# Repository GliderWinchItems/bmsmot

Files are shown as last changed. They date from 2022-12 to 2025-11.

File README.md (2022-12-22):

# bmsmot
This board is the control for the BMS (battery monitoring system) for one string of batteries; the contactor function, thermistor inputs for motor coolant, and output drive for enables, relays, and external high current FET sub-boards. A STM32F446RET6 is the main processor on this board.

The contactor function measures the high voltage using a STM32L431RCT6, ground isolated and communicates readings to the main processor via uart with opto-isolator. It also measures battery string current using an external Hall-effect sensor.

The main board provides for the CAN bus cabling to the BMS modules to loop back and apply +12v current to both ends of the CAN cabling, as well as in & out connectors for other nodes on the CAN bus. Provision is for a second CAN bus.

The software provides the EMC (Energy Management Control) and MMC (Motor Management Control) functions for one battery/motor installation.

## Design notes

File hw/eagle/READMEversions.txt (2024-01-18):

READMEversions.txt
12/27/23

pwrfet

1. Initial board (5 boards ordered): 

  TLP151A blew up twice, 

  AUIRS2110S didn't work...twice. 

  Motor transients appeared to cause at least
one blowup.

  Hacked (ugly) to add 12v regulator--
  - No fet driver
  - SB540 diode flyback
  - works

2. pwrfet-v2 (5 boards ordered)

First version but added 
  12v regulator (two options)
  DGD05463 FET driver
  Misc improvements of caps foot prints, etc.

 Polarity incorrect on fet driver incorrect.
  Solution 1: motor hi/lo junction to ground
   instead of +12 to hi/lo junction.
  Solution 2: remove fet3 and drive TLP151
    directly from bmsmot board's 74HCT125.

3. pwrfet-v3 (5 boards ordered)

V2 revised for ADP3110 or ADP3120 FET driver
which is a SOT package

Polarity incorrect to fet driver (same as v2).
 1st board: removed driver and hi side fet,
   diode flyback. 
   TLP151 drives lo side fet directly.

4. pwrfet-v4 (layout not complete as of 12/27/23)

V3 revised to add 74HCT02 (quad NOR) and AP311 comparator
to limit max current in low-side FET source.

5. pfuart & pfCAN

New repo started for a version using a STM32L431.
See: GliderWinchItems/isopwrfet.

  pfCAN layout complete (240109) but not reviewed.

  pfuart not started work.

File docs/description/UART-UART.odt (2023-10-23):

Goal: Send/receive CAN msgs over UART-UART comm connection between two processors.

Conditions & Restrictions:

1. 1 Mbps rate

2. No char-by-char interrupt allowed (which means only DMA)

3. Fixed block/packet size (19 bytes)

- start byte

- 16 data bytes (CAN struct: ID, DRC, Payload)

- check byte

- stop byte

4. Start/Stop phasing

- Initialization may begin in the middle of a packet being received, and possibility is high.

- Noise may cause start/stop phasing may be lost during operation, but possibility is low.

5. Check byte error

- Used to determine if the packet is legitimate when a stop byte 18 bytes following a start byte is encountered.

- Make use of STM32 hardware CRC peripheral.

6. Minimize packets lost when re-syncing.

General scheme--

Make use of STM32F446 double buffering DMA.

- Two registers for start of storing USART2-RX: S5MOAR S5SM1AR

Before enable both registers may be written.

After enable the register not being used to store can be written. The CT bit 19 in the S5CR (Control Register)

0: current target memory is Memory 0 (addressed by the DMA_SxM0AR pointer)

1: current target memory is Memory 1 (addressed by the DMA_SxM1AR pointer)

- Set the buffer size (S5NDTR) to 2*packet size (i.e. 2*19=38).

- Set circular mode. Pointer and size reloads when end of buffer reached.

- Enable Half and Full interrupts. This will give an interrupt at every 19 bytes stored, i.e. the packet size.

If the start of packet is in synch so that the first byte of the buffer and byte following the half buffer are start bytes and the stop and check bytes are OK, then the DMA will give an interrupt every time a complete CAN msg has been received. The half and full interrupts allow the previously stored ½ buffer to be processed while new incoming bytes are being stored. Basically, an interrupt after each CAN msg has been received.

The tricky problem is how to get the DMA in sync with the start of the packets without resorting to char-by-char uart interrupts.

To do char-by-char interrupts requires the interrupt priority to be higher than the RTOS timer, since it could preempt handing a char interrupt and cause on overrun. Also, the shear speed, especially if there are two UARTs running is a heavy processor load. One char for USART2 at 1 Mbps is 10 usec. Hence, reliance of the DMA is required.

To resync, the plan is to make use of the option to change the address where the buffer pointer not currently in use can be updated.

Suppose the buffers are laid out as follows--

#define B_START 0x36; // Unlikely noise triggered char

#define B_STOP ~START

struct UCAN

{

uint8 start;

struct CANRCVBUF

uint16 pec15

uint8 stop;

};

struct UCAN uubuf[2*3];

Two pairs of UCAN buffers.

Hmm, does there need to be an overrun, i.e. “3”.

S5M0AR = &uubuf[0];

S5M1AR = &uubuf[2];

S5NDTR = sizeof(struct UCAN);

06/08/2023 UART-UART communication Page 2

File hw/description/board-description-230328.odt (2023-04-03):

Overview

The following describes the bmsmot pcb design & layout at this stage of development (March 31 2023). The eagles files can be found in--

~/GliderWinchItems/bmsmot/hw/eagle/bmsmot

Only parts for the needed features can be installed, and the value of resistors, capacitors, etc., the following are tentative and depend upon the assignments.

This board can be configured to handle the EMC/MMC or PSN Power Supply Node (PSN).

For the EMC/MMC the following is supplied

- BMS CAN 12v power switched

- BMS CAN Master Reset switched

- Contactor coil #1 energize

- Contactor coil #2 energize

- Contactor HV measurements

- Contactor current measurements

- Cooling pump control (PWM)

- Heat exchanger fan/blower control (PWM)

- DMOC fan control (PWM)

- SCP 12v supply input on/off relay

- RCP 12v supply input on/off relay

- SCP 12v supply output relay on/off

- AC/DC input power select relay

- Coolant inlet temperature thermistor

- Coolant outlet temperature thermistor

- Ambient temperature thermistor

- Float battery string leakage detection

For PSN-

- Main 12v battery on/off

- Air compressor on/off

- Air pressure measurement (ADC)

- AC voltage measurement

- Mains|generator select

- RTC wakeup

- Rotating beacon

Other provisions-

- LEDs

LED1 - Green: 12v switched power

LED2 – Green: PB12 i/o-F446

LED3 – Red: PB13 i/o-F446

LED4 – Green: PB0 i/o- L431

LED5 – Red: PB1 i/o-L431

LED6 – Red: NFET5-PA5-Master Reset or Master Reset pushbutton (BMS loop)

- EMC/MMC-local to EMC-master UART-UART communication option

- Pushbuttons

RESET – F446

RESET – L431

Master-Reset BMS loop

- Header for encoder (TIM2)

- ADC: F446: six with headers

Four with 2 pin headers: 10K pullup w 0.1 cap to gnd

+12v power measurement (no header)

One with 2 pin header: Series resistor, 10K pullup w 0.1 cap to gnd

One with 3 pin header: Resistor divider (5V→3.3V) w big cap to gnd.

- ADC: F446: 12v switched power voltage measurement

- spare FET output

JP20 - 2-pin header, NFET-SUB14, PB3- T2C2

- Xtals:Oscillators

32 Khz RTC

16 MHz system

Board size

140 x 100 mm

Mounting hole (dia 3.2 mm) positions--

3.2 3.2

136.8 3.2

136.8 96.8

3.2 96.8

80.0 70.0

12v power input

(Upper-left) the 12v power is connected via a Power Pole connector pair with a pigtail, or spade lugs. There are two large holes for strain relief for the Power Pole option. The pigtail solders into holes in the middle of the spade lug thu-holes. This called the “raw” 12v power.

Possible power PFETs provide polarity protection--

DMP3007SCG-7

PJQ4403

The input voltage will exceed the Vgs for a DMP3007 so a 10v zener used. The PJQ4403 has a +/- 20 Vgs so the zener could be omitted, however the PJQ4403 has a lower continuous Id.

The polarity protection PFET limits the total current to about 4a. That includes the BMS loop and any +12v loads one the headers, e.g. relays, plus the processor load. Each of the BMS low current chargers can draw about 6W. A string of six requires 36W, or about 3a at 12v.

12V power protected

The polarity protected output of the input PFET is “+12V” on the schematic. This feeds into a second PFET that can switch the 12v on/off.

12V power switched

The switched 12v feeds the BMS CAN bus loop, and most of the BMS board.

When configured for a Power Supply Node (PSN) the 12v battery would power this board and if the second PFET is off the only load on the battery is the 5v regulator and processor. The processor would be in shutdown mode so its draw would be in the 1-10 ua range. The linear regulator is 1.8 ua typical. To wake the system, either a short to gnd via the 2-pin header JP19, or NFET1 turned on via the processor RTC and coin-cell.

Configured for the EMC/MMC the switched 12v can turn the BMS CAN bus 12v on/off via the NFET and i/o pin PC13.

FET outputs (SUBx)

Eight FET driven outputs are labeled HDR-SUB1 through HDR-SUB8. Each output has a JST 4 pin keyed header (gnd, fet drain, +5v, +12v). Provision is for flyback diodes to 5v, 12v, and a pullup resistor. The FET, diode/resistor, installed depends on the usage of the output.

Each FET is driven from an i/o pin that can be assigned to a timer channel so that PWM can be applied. Some outputs share the same timer which means that the PWM frame duration would be common to all the channels on that timer doing PWM.

pcb label: i/o - timer:channel

HDR-SUB1: PB2 - T2C4

HDR-SUB2: PB10 - T2C3

HDR-SUB3: PB14 - T12C1

HDR-SUB4: PB15 - T12C2

HDR-SUB5: PC6 – T3C1, T8C1

HDR-SUB6: PC7 – T3C2, T8C2

HDR-SUB7: PC8 – T3C3, T8C3

HDR-SUB8: PC9 – T3C4, T8C4

Note: if the encoder input is used (TIM2) there could be some time frame issues if HDR-SUB1 & 2 assignments are for PWMing.

FET outputs (HDRx)

Four outputs driven by a 74VHCT125 buffers can drive external sub-boards with power fets for high current switching. These inputs to the buffers are i/o pins that have associated timers.

HDRXX1: PA10 - T1C3

HDRXX2: PA11 - T1C4

HDRXX3: PA9 - T1C2

HDRXX4: PA8 - T1C1

ADC ‘F446

Eight ADC channels with headers used.

Four inputs have 10K pullups and 0.1u cap to gnd for thermistors.

JP1 – PC0-ADC123-IN10

JP8 – PC1-ADC123-IN11

JP9 - PC2-ADC123-IN12

JP10 - PC3-ADC123-IN13

One has a series resistor added which could be used for voltage divider by installing a resistor in place of the 0.1 cap. It could be used for input of an external switch or contacts; the 0.1 cap could be replaced with a zener if voltage protection is needed, etc.

JP22 -PC4-ADC12-IN14

One with a keyed 3 pin JST connector, JP24 (gnd, signal, +5v), for air pressure sensor. The +5 is from the dc-dc switcher for the main board so it has some switching ripple on it. The signal line has a resistor divider (R36|R19) for reducing the max voltage to 3.3v, and 4.6u 0603 cap (C38) can be used to help the noise, along with software filtering.

JP24 – PC5-ADC12-IN15

Battery string leakage detection

To keep the battery string from accumulating charge and drifting too far above/below the system ground to where the isolation components (e.g. CAN interfaces and dc-dc converters) voltage isolation will be exceed, two large resistors (22M), plus divider shunt resistors (110K), tie the battery string plus and minus to system ground, so that the battery string is minus and plus are equal voltages to the system ground, i.e. approximately +/- 200 volts if the string is at 400v charge.

To fall within the worst-case working voltage limit the resistors need to be 1W. These are thru-hole resistors (R38, R39).

The header for the contactor HV connections has an additional pin for connection directly to the battery plus, and is on the battery string side of the contactor so it is always connected. At ~22M for each battery leg to ground the current drain at 440v is 22 ua.

The battery string plus and minus dividers, feed a very low bias current (1 pa) dual op-amp (TLV522) and the op-amp outputs feed PB0-ADC12-IN8 and PB1-ADC12-IN9. The software can compare the voltage readings and signal when the imbalance exceeds a threshold that signals leakage in the battery/DMOC/motor system.

Master-Reset

The BMS loop RJ45 jack pair OR the Master-Reset from the CAN1 bus, presumably pulled to gnd by the system CAN bus, and the NFET or pushbutton. The NFET can pull the Master-Reset for the BMS CAN bus loop to gnd without affecting the Master-Reset line on the CAN1 bus.

The pushbutton is mostly for sw debugging and test, and probably not worth installing on all boards. Pressing the pushbutton pulls the Master-Reset for the BMS loop to gnd, resetting all BMS boards on the loop. Other boards on the loop that have the Master-Reset feature would also be reset, but non-BMS boards on the loop are not contemplated.

Red LED6 lights when the BMS loop Master-Reset is pull to gnd.

Coin-cell and VBAT

A vertical socket for a CR2032 coin-cell (upper right corner of pcb) powers VBAT. When the coin-cell is present and the voltage is above 1.7v the RTC domain of the ‘F446 remains active when the processor power is off.

VBAT is internally connected with a diode to Vcc inside the processor so when the coin-cell is not installed the RTC section still works when the processor is powered, however it is recommended that when there is no coin-cell that VBAT be connected to VCC. No reason is given as to why this is recommended. One could speculate that given the extremely low current draw of the VBAT that a floating pin when the power is off might end up with some breakdown of internal circuits. A resistor (which could be zero ohm) to connect VBAT to Vcc is provided.

The RTC section when maintained by the coin-cell will run the 32 Khz clock, power a few i/o pins and power the backup registers (1K bytes). The RTC timer can be configured to have PC13 raise the NFET to switch the +12V on when there is a timeout. The NFET is OR’d with a 2 pin hdr so that a jumper or external switch will pull the power PFET gate down to turn on the +12v.

Isolated ‘L431

A STM32L431RxT6 processor is isolated from the system ground. Since the 5v-5v isolation is switcher and noisy (and the input to the dc-dc isolation switcher is also a switcher output) linear regulators are used to clean up the power. Two 5v-5v 1W converters are used. The output of the two converters are connected in series to provide a nominal 10v which is linear regulated to 5v to provide a clean 5v for a Hall-effect current sensor. The first dc-dc converter output is linear regulated to drive the processor 3.3v and its ADC.

Provision is for four high voltage dividers to the ADC. The resistor to the high voltage is a thru-hole resistor as the working voltage spec requires ½ watt resistor.

For filtering, the HV resistor is 1M with a series 110K to the ADC pin with 10K ADC pin to gnd shunt. The 1M and 110K junction has 0.1u cap and the ADC pin has a 0.1u to gnd cap.

Header for Hall-effect (gnd, signal, +5) with the signal going through a filter of 0.1u-series 5.6K-0.1u-10K to with ADC pin with 0.1u to gnd.

A processor i/o pin driven red and green LED are for debugging/trouble-shooting.

The SWD and FTDI headers provide for flashing and debugging.

Isolated UART TX & RX is provided. The ‘L431-to-’F446 direction is necessary for streaming readings; the reverse direction might be used for possible program updating over CAN.

Additions (that complete the usage of all pins)

PB4: General purpose JIC input. Two 0603 resistors are shown on the schematic, but the shunt one might be changed to a cap, or a zener.

PA12: Thru-hole solder pad

PA15: Thru-hole solcer pad

Sub-board: pwrfet

This sub-board has an isolated high current NFET pair for PWM or ON/OFF drive of high current loads. The high-side fet acts as a low drop flyback diode. A HDRXX output of the bmsmot board drives a small NFET on this sub-board which drives an opto isolated FET driver which then drives the high current fet pair.

The high current NFET, IRFS3007-7 is obsolete, but 24 are on hand. It has a 60v 210a max rating. The FET driver is AUIRS2110S and also on hand. The isolated driver is TLP151A (not on-hand).

The AUIRS2110S limits the 12v input voltage to 20v; the TLP151A 30v. Minimum is 10v, and at 10v the minimum output of the TLP151A (8.5v) might not meet the minimum high input (9.5v) TLP151A to produce a high enough voltage to turn on the AUIRS2110S. At 11v it should meet the specs.

The 12v power and load connections can be made with a Power Pole pair of connectors and pigtail that goes though strain relief holes. Thru-holes for spade lugs are also provided.

The layout has large vias for the plus and minus 12v power. Multiple sub-boards could be connected side-by-side and heavy wire jumpers daisy-chain the 12v power. Doing this would cut to the 12v Power Pole connector requirements to just one.

Page 6 03/29/23 PCB description

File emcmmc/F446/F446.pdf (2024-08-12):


12/08/2024

## F446 Project Configuration Report

# 1. Description

## 1.1. Project

Project Name | F446
Board Name | custom
Generated with: | STM32CubeMX 6.3.0
Date | 08/12/2024

## 1.2. MCU

MCU Series | STM32F4
MCU Line | STM32F446
MCU name | STM32F446RETx
MCU Package | LQFP64
MCU Pin number | 64

## 1.3. Core(s) information

Core(s) | Arm Cortex-M4

# 2. Pinout Configuration

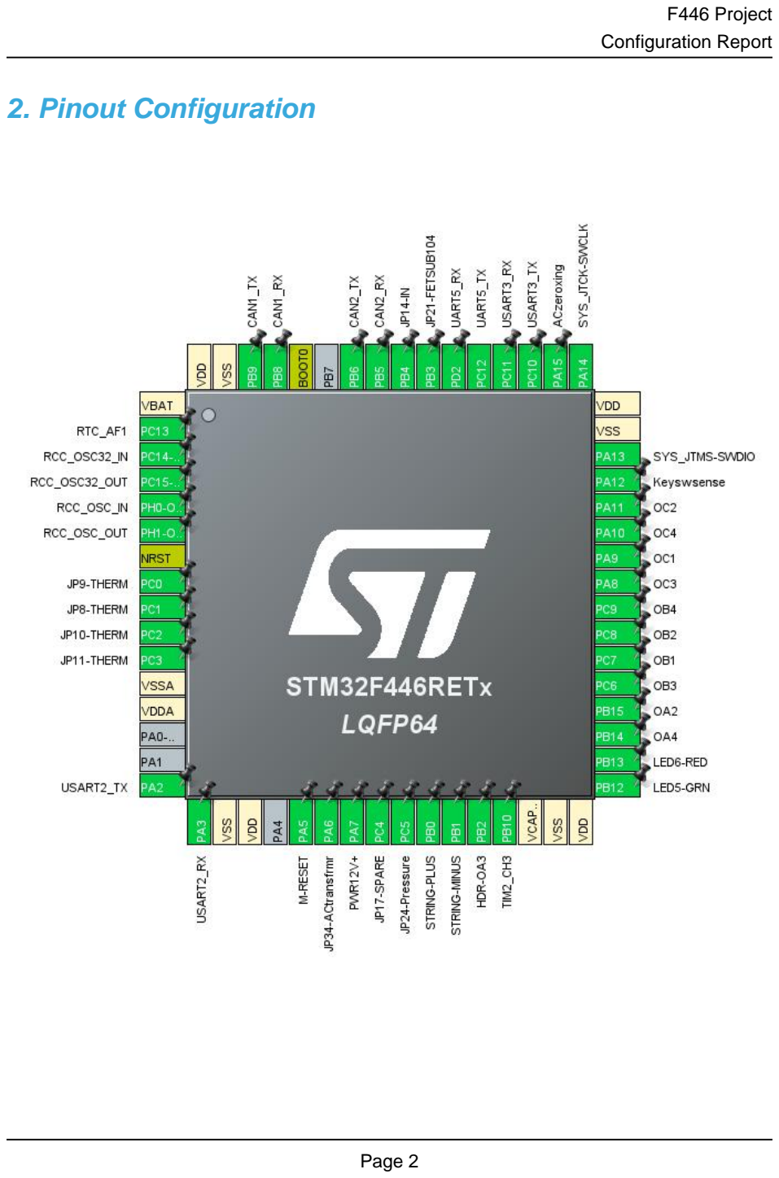
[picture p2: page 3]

# 3. Pins Configuration

Pin Number LQFP64 | Pin Name (function after reset) | Pin Type | Alternate Function(s) | Label
1 | VBAT | Power
2 | PC13 | I/O | RTC_AF1
3 | PC14-OSC32_IN | I/O | RCC_OSC32_IN
4 | PC15-OSC32_OUT | I/O | RCC_OSC32_OUT
5 | PH0-OSC_IN | I/O | RCC_OSC_IN
6 | PH1-OSC_OUT | I/O | RCC_OSC_OUT
7 | NRST | Reset
8 | PC0 | I/O | ADC3_IN10, ADC1_IN10 | JP9-THERM
9 | PC1 | I/O | ADC2_IN11, ADC3_IN11, ADC1_IN11 | JP8-THERM
10 | PC2 | I/O | ADC2_IN12, ADC3_IN12, ADC1_IN12 | JP10-THERM
11 | PC3 | I/O | ADC1_IN13 | JP11-THERM
12 | VSSA | Power
13 | VDDA | Power
16 | PA2 | I/O | USART2_TX
17 | PA3 | I/O | USART2_RX
18 | VSS | Power
19 | VDD | Power
21 | PA5 * | I/O | GPIO_Output | M-RESET
22 | PA6 | I/O | ADC1_IN6, ADC2_IN6 | JP34-ACtransfrmr
23 | PA7 | I/O | ADC1_IN7 | PWR12V+
24 | PC4 | I/O | ADC1_IN14 | JP17-SPARE
25 | PC5 | I/O | ADC2_IN15, ADC1_IN15 | JP24-Pressure
26 | PB0 | I/O | ADC1_IN8 | STRING-PLUS
27 | PB1 | I/O | ADC1_IN9 | STRING-MINUS
28 | PB2 | I/O | TIM2_CH4 | HDR-OA3
29 | PB10 | I/O | TIM2_CH3
30 | VCAP_1 | Power
31 | VSS | Power
32 | VDD | Power
33 | PB12 * | I/O | GPIO_Output | LED5-GRN
34 | PB13 * | I/O | GPIO_Output | LED6-RED
35 | PB14 | I/O | TIM12_CH1 | OA4
36 | PB15 | I/O | TIM12_CH2 | OA2
37 | PC6 | I/O | TIM3_CH1 | OB3

Pin Number LQFP64 | Pin Name (function after reset) | Pin Type | Alternate Function(s) | Label
38 | PC7 | I/O | TIM3_CH2 | OB1
39 | PC8 | I/O | TIM3_CH3 | OB2
40 | PC9 | I/O | TIM3_CH4 | OB4
41 | PA8 | I/O | TIM1_CH1 | OC3
42 | PA9 | I/O | TIM1_CH2 | OC1
43 | PA10 | I/O | TIM1_CH3 | OC4
44 | PA11 | I/O | TIM1_CH4 | OC2
45 | PA12 * | I/O | GPIO_Input | Keyswsense
46 | PA13 | I/O | SYS_JTMS-SWDIO
47 | VSS | Power
48 | VDD | Power
49 | PA14 | I/O | SYS_JTCK-SWCLK
50 | PA15 | I/O | GPIO_EXTI15 | ACzeroxing
51 | PC10 | I/O | USART3_TX
52 | PC11 | I/O | USART3_RX
53 | PC12 | I/O | UART5_TX
54 | PD2 | I/O | UART5_RX
55 | PB3 | I/O | TIM2_CH2 | JP21-FETSUB104
56 | PB4 * | I/O | GPIO_Input | JP14-IN
57 | PB5 | I/O | CAN2_RX
58 | PB6 | I/O | CAN2_TX
60 | BOOT0 | Boot
61 | PB8 | I/O | CAN1_RX
62 | PB9 | I/O | CAN1_TX
63 | VSS | Power
64 | VDD | Power

## * The pin is affected with an I/O function

# 4. Clock Tree Configuration

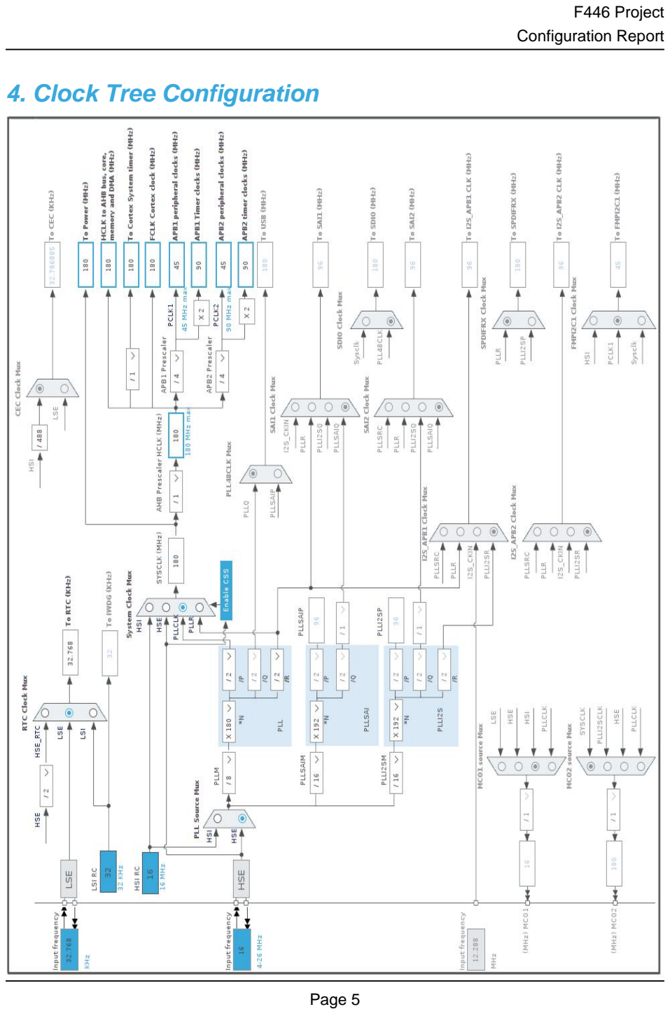
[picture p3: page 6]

# 5. Software Project

## 5.1. Project Settings

Name | Value
Project Name | F446
Project Folder | /home/deh/GliderWinchItems/bmsmot/emcmmc/F446
Toolchain / IDE | Makefile
Firmware Package Name and Version | STM32Cube FW_F4 V1.26.2
Application Structure | Advanced
Generate Under Root | No
Do not generate the main() | No
Minimum Heap Size | 0x200
Minimum Stack Size | 0x400

## 5.2. Code Generation Settings

Name | Value
STM32Cube MCU packages and embedded software | Copy all used libraries into the project folder
Generate peripheral initialization as a pair of '.c/.h' files | No
Backup previously generated files when re-generating | No
Keep User Code when re-generating | Yes
Delete previously generated files when not re-generated | Yes
Set all free pins as analog (to optimize the power consumption) | No
Enable Full Assert | No

## 5.3. Advanced Settings - Generated Function Calls

Rank | Function Name | Peripheral Instance Name
1 | SystemClock_Config | RCC
2 | MX_GPIO_Init | GPIO
3 | MX_DMA_Init | DMA
4 | MX_CAN1_Init | CAN1
5 | MX_CAN2_Init | CAN2
6 | MX_UART5_Init | UART5
7 | MX_USART2_UART_Init | USART2
8 | MX_USART3_UART_Init | USART3
9 | MX_TIM1_Init | TIM1
10 | MX_TIM2_Init | TIM2
11 | MX_ADC1_Init | ADC1

Rank | Function Name | Peripheral Instance Name
12 | MX_TIM3_Init | TIM3
13 | MX_TIM12_Init | TIM12
14 | MX_TIM5_Init | TIM5
15 | MX_TIM13_Init | TIM13
16 | MX_TIM9_Init | TIM9
17 | MX_ADC2_Init | ADC2
18 | MX_RTC_Init | RTC

# 6. Power Consumption Calculator report

## 6.1. Microcontroller Selection

Series | STM32F4
Line | STM32F446
MCU | STM32F446RETx
Datasheet | DS10693_Rev6

## 6.2. Parameter Selection

Temperature | 25
Vdd | 3.3

## 6.3. Battery Selection

Battery | Li-SOCL2(A3400)
Capacity | 3400.0 mAh
Self Discharge | 0.08 %/month
Nominal Voltage | 3.6 V
Max Cont Current | 100.0 mA
Max Pulse Current | 200.0 mA
Cells in series | 1
Cells in parallel | 1

## 6.4. Sequence

Step | Step1 | Step2
Mode | RUN | STOP_UDM (Under Drive)
Vdd | 3.3 | 3.3
Voltage Source | Battery | Battery
Range | Scale1-High | No Scale
Fetch Type | RAM/FLASH/REGON/ART/P REFETCH | n/a
CPU Frequency | 180 MHz | 0 Hz
Clock Configuration | HSE PLL | Regulator_LP Flash-PwrDwn
Clock Source Frequency | 4 MHz | 0 Hz

### Peripherals

Additional Cons. | 0 mA | 0 mA
Average Current | 46 mA | 55 µA
Duration | 0.1 ms | 0.9 ms
DMIPS | 225.0 | 0.0
Ta Max | 98.02 | 104.99
Category | In DS Table | In DS Table

## 6.5. Results

Sequence Time | 1 ms | Average Current | 4.65 mA
Battery Life | 1 month | Average DMIPS | 225.0 DMIPS

## 6.6. Chart

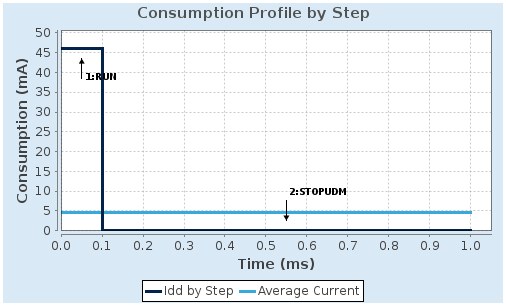
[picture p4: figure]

# 7. Peripherals and Middlewares Configuration

## 7.1. ADC1 mode: IN7 mode: IN8 mode: IN9 mode: IN10 mode: IN11 mode: IN12 mode: IN13 mode: IN14 mode: IN15 mode: Vrefint Channel mode: Vbat Channel

## 7.1.1. Parameter Settings:

### ADCs_Common_Settings:

Mode | Independent mode

### ADC_Settings:

Clock Prescaler | PCLK2 divided by 4 *
Resolution | 12 bits (15 ADC Clock cycles)
Data Alignment | Right alignment
Scan Conversion Mode | Enabled
Continuous Conversion Mode | Enabled *
Discontinuous Conversion Mode | Disabled
DMA Continuous Requests | Enabled *
End Of Conversion Selection | EOC flag at the end of single channel conversion

### ADC_Regular_ConversionMode:

Number Of Conversion | 12 *
External Trigger Conversion Source | Regular Conversion launched by software
External Trigger Conversion Edge | None
Rank | 1
Channel | Channel 10 *
Sampling Time | 56 Cycles *
Rank | 2 *
Channel | Channel 11 *
Sampling Time | 56 Cycles *
Rank | 3 *

Channel | Channel 12 *
Sampling Time | 56 Cycles *
Rank | 4 *
Channel | Channel 13 *
Sampling Time | 56 Cycles *
Rank | 5 *
Channel | Channel 14 *
Sampling Time | 56 Cycles *
Rank | 6 *
Channel | Channel 15 *
Sampling Time | 56 Cycles *
Rank | 7 *
Channel | Channel 7
Sampling Time | 144 Cycles *
Rank | 8 *
Channel | Channel 8 *
Sampling Time | 56 Cycles *
Rank | 9 *
Channel | Channel 9 *
Sampling Time | 56 Cycles *
Rank | 10 *
Channel | Channel 7
Sampling Time | 144 Cycles *
Rank | 11 *
Channel | Channel Vbat *
Sampling Time | 480 Cycles *
Rank | 12 *
Channel | Channel Vrefint *
Sampling Time | 480 Cycles *

### ADC_Injected_ConversionMode:

Number Of Conversions | 0

### WatchDog:

Enable Analog WatchDog Mode | false

## 7.2. ADC2 mode: IN6

## 7.2.1. Parameter Settings:

### ADCs_Common_Settings:

Mode | Independent mode

### ADC_Settings:

Clock Prescaler | PCLK2 divided by 4 *
Resolution | 12 bits (15 ADC Clock cycles)
Data Alignment | Right alignment
Scan Conversion Mode | Enabled *
Continuous Conversion Mode | Enabled
Discontinuous Conversion Mode | Disabled
DMA Continuous Requests | Enabled *
End Of Conversion Selection | EOC flag at the end of all conversions *

### ADC_Regular_ConversionMode:

Number Of Conversion | 1
External Trigger Conversion Source | Regular Conversion launched by software
External Trigger Conversion Edge | None
Rank | 1
Channel | Channel 6
Sampling Time | 56 Cycles *

### ADC_Injected_ConversionMode:

Number Of Conversions | 0

### WatchDog:

Enable Analog WatchDog Mode | false

## 7.3. CAN1 mode: Activated

## 7.3.1. Parameter Settings:

### Bit Timings Parameters:

Prescaler (for Time Quantum) | 9 *
Time Quantum | 200.0 *
Time Quanta in Bit Segment 1 | 7 Times *
Time Quanta in Bit Segment 2 | 2 Times *
Time for one Bit | 2000.00 *

Baud Rate | 500000 *
ReSynchronization Jump Width | 1 Time

### Basic Parameters:

Time Triggered Communication Mode | Disable
Automatic Bus-Off Management | Disable
Automatic Wake-Up Mode | Disable
Automatic Retransmission | Enable *
Receive Fifo Locked Mode | Disable
Transmit Fifo Priority | Disable

### Advanced Parameters:

Operating Mode | Normal

## 7.4. CAN2 mode: Activated

## 7.4.1. Parameter Settings:

### Bit Timings Parameters:

Prescaler (for Time Quantum) | 10 *
Time Quantum | 222.22222222222223 *
Time Quanta in Bit Segment 1 | 6 Times *
Time Quanta in Bit Segment 2 | 2 Times *
Time for one Bit | 1999.99 *
Baud Rate | 500000 *
ReSynchronization Jump Width | 2 Times *

### Basic Parameters:

Time Triggered Communication Mode | Disable
Automatic Bus-Off Management | Disable
Automatic Wake-Up Mode | Disable
Automatic Retransmission | Enable *
Receive Fifo Locked Mode | Disable
Transmit Fifo Priority | Disable

### Advanced Parameters:

Operating Mode | Normal

## 7.5. RCC

## High Speed Clock (HSE): Crystal/Ceramic Resonator Low Speed Clock (LSE) : Crystal/Ceramic Resonator

## 7.5.1. Parameter Settings:

### System Parameters:

VDD voltage (V) | 3.3
Instruction Cache | Enabled
Prefetch Buffer | Enabled
Data Cache | Enabled
Flash Latency(WS) | 5 WS (6 CPU cycle)

### RCC Parameters:

HSI Calibration Value | 16
TIM Prescaler Selection | Disabled
HSE Startup Timout Value (ms) | 100
LSE Startup Timout Value (ms) | 5000

### Power Parameters:

Power Regulator Voltage Scale | Power Regulator Voltage Scale 1
Power Over Drive | Enabled

## 7.6. RTC mode: Activate Clock Source WakeUp: Routed to AF1

## 7.6.1. Parameter Settings:

### General:

Hour Format | Hourformat 24
Asynchronous Predivider value | 127
Synchronous Predivider value | 255
Output Polarity | Output Polarity High
Output Type | Output Type Opendrain

### Calendar Time:

Data Format | BCD data format
Hours | 0
Minutes | 0
Seconds | 0
Day Light Saving: value of hour adjustment | Daylightsaving None
Store Operation | Storeoperation Reset

### Calendar Date:

Week Day | Monday

Month | January
Date | 1
Year | 0

### Wake UP:

Wake Up Clock | RTCCLK / 16
Wake Up Counter | 0

## 7.7. SYS Debug: Serial Wire Timebase Source: TIM14

## 7.8. TIM1 Clock Source : Internal Clock Channel1: PWM Generation CH1 Channel2: PWM Generation CH2 Channel3: PWM Generation CH3 Channel4: PWM Generation CH4

## 7.8.1. Parameter Settings:

### Counter Settings:

Prescaler (PSC - 16 bits value) | 0
Counter Mode | Up
Counter Period (AutoReload Register - 16 bits value ) | 18000 *
Internal Clock Division (CKD) | No Division
Repetition Counter (RCR - 8 bits value) | 0
auto-reload preload | Disable

### Trigger Output (TRGO) Parameters:

Master/Slave Mode (MSM bit) | Disable (Trigger input effect not delayed)
Trigger Event Selection | Reset (UG bit from TIMx_EGR)

### Break And Dead Time management - BRK Configuration:

BRK State | Disable
BRK Polarity | High

### Break And Dead Time management - Output Configuration:

Automatic Output State | Disable
Off State Selection for Run Mode (OSSR) | Disable
Off State Selection for Idle Mode (OSSI) | Disable
Lock Configuration | Off

### PWM Generation Channel 1:

Mode | PWM mode 1
Pulse (16 bits value) | 0
Output compare preload | Enable
Fast Mode | Disable
CH Polarity | High
CH Idle State | Reset

### PWM Generation Channel 2:

Mode | PWM mode 1
Pulse (16 bits value) | 0
Output compare preload | Enable
Fast Mode | Disable
CH Polarity | High
CH Idle State | Reset

### PWM Generation Channel 3:

Mode | PWM mode 1
Pulse (16 bits value) | 0
Output compare preload | Enable
Fast Mode | Disable
CH Polarity | High
CH Idle State | Reset

### PWM Generation Channel 4:

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

## 7.9. TIM2 Clock Source : Internal Clock Channel2: PWM Generation CH2 Channel3: PWM Generation CH3 Channel4: PWM Generation CH4

## 7.9.1. Parameter Settings:

### Counter Settings:

Prescaler (PSC - 16 bits value) | 2 *
Counter Mode | Up
Counter Period (AutoReload Register - 32 bits value ) | 18000 *

Internal Clock Division (CKD) | No Division
auto-reload preload | Disable

### Trigger Output (TRGO) Parameters:

Master/Slave Mode (MSM bit) | Disable (Trigger input effect not delayed)
Trigger Event Selection | Reset (UG bit from TIMx_EGR)

### PWM Generation Channel 2:

Mode | PWM mode 1
Pulse (32 bits value) | 0
Output compare preload | Enable
Fast Mode | Disable
CH Polarity | High

### PWM Generation Channel 3:

Mode | PWM mode 1
Pulse (32 bits value) | 0
Output compare preload | Enable
Fast Mode | Disable
CH Polarity | High

### PWM Generation Channel 4:

Mode | PWM mode 1
Pulse (32 bits value) | 0
Output compare preload | Enable
Fast Mode | Disable
CH Polarity | High

## 7.10. TIM3 Clock Source : Internal Clock Channel1: PWM Generation CH1 Channel2: PWM Generation CH2 Channel3: PWM Generation CH3 Channel4: PWM Generation CH4

## 7.10.1. Parameter Settings:

### Counter Settings:

Prescaler (PSC - 16 bits value) | 0
Counter Mode | Up
Counter Period (AutoReload Register - 16 bits value ) | 18000 *
Internal Clock Division (CKD) | No Division
auto-reload preload | Disable

### Trigger Output (TRGO) Parameters:

Master/Slave Mode (MSM bit) | Disable (Trigger input effect not delayed)
Trigger Event Selection | Reset (UG bit from TIMx_EGR)

### PWM Generation Channel 1:

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

### PWM Generation Channel 2:

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

### PWM Generation Channel 3:

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

### PWM Generation Channel 4:

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

## 7.11. TIM5 mode: Clock Source Channel1: Output Compare No Output

## 7.11.1. Parameter Settings:

### Counter Settings:

Prescaler (PSC - 16 bits value) | 9000 *
Counter Mode | Up
Counter Period (AutoReload Register - 32 bits value ) | 4294967295
Internal Clock Division (CKD) | No Division
auto-reload preload | Disable

### Trigger Output (TRGO) Parameters:

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

### Output Compare No Output Channel 1:

Mode | Frozen (used for Timing base)
Pulse (32 bits value) | 0
Output compare preload | Disable
CH Polarity | High

## 7.12. TIM9 mode: Clock Source mode: One Pulse Mode

## 7.12.1. Parameter Settings:

### Counter Settings:

Prescaler (PSC - 16 bits value) | 9000 *
Counter Mode | Up
Counter Period (AutoReload Register - 16 bits value ) | 65535
Internal Clock Division (CKD) | No Division
auto-reload preload | Disable

## 7.13. TIM12 mode: Clock Source Channel1: PWM Generation CH1 Channel2: PWM Generation CH2

## 7.13.1. Parameter Settings:

### Counter Settings:

Prescaler (PSC - 16 bits value) | 0
Counter Mode | Up
Counter Period (AutoReload Register - 16 bits value ) | 18000 *
Internal Clock Division (CKD) | No Division
auto-reload preload | Disable

### PWM Generation Channel 1:

Mode | PWM mode 1
Pulse (16 bits value) | 0
Output compare preload | Enable
Fast Mode | Disable

CH Polarity | High

### PWM Generation Channel 2:

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

## 7.14. TIM13 mode: Activated Channel1: Output Compare No Output

## 7.14.1. Parameter Settings:

### Counter Settings:

Prescaler (PSC - 16 bits value) | 9000 *
Counter Mode | Up
Counter Period (AutoReload Register - 16 bits value ) | 65535
Internal Clock Division (CKD) | No Division
auto-reload preload | Disable

### Output Compare No Output Channel 1:

Mode | Frozen (used for Timing base)
Pulse (16 bits value) | 0
Output compare preload | Disable
CH Polarity | High

## 7.15. UART5 Mode: Asynchronous

## 7.15.1. Parameter Settings:

### Basic Parameters:

Baud Rate | 115200
Word Length | 8 Bits (including Parity)
Parity | None
Stop Bits | 1

### Advanced Parameters:

Data Direction | Receive Only *
Over Sampling | 16 Samples

## 7.16. USART2 Mode: Asynchronous

## 7.16.1. Parameter Settings:

### Basic Parameters:

Baud Rate | 115200
Word Length | 8 Bits (including Parity)
Parity | None
Stop Bits | 1

### Advanced Parameters:

Data Direction | Receive and Transmit
Over Sampling | 16 Samples

## 7.17. USART3 Mode: Asynchronous

## 7.17.1. Parameter Settings:

### Basic Parameters:

Baud Rate | 115200
Word Length | 8 Bits (including Parity)
Parity | None
Stop Bits | 1

### Advanced Parameters:

Data Direction | Receive and Transmit
Over Sampling | 16 Samples

## 7.18. FREERTOS Interface: CMSIS_V1

## 7.18.1. Config parameters:

### API:

FreeRTOS API | CMSIS v1

### Versions:

FreeRTOS version | 10.3.1

CMSIS-RTOS version | 1.02

### MPU/FPU:

ENABLE_MPU | Disabled
ENABLE_FPU | Disabled

### Kernel settings:

USE_PREEMPTION | Enabled
CPU_CLOCK_HZ | SystemCoreClock
TICK_RATE_HZ | 1000
MAX_PRIORITIES | 7
MINIMAL_STACK_SIZE | 128
MAX_TASK_NAME_LEN | 16
USE_16_BIT_TICKS | Disabled
IDLE_SHOULD_YIELD | Enabled
USE_MUTEXES | Enabled
USE_RECURSIVE_MUTEXES | Disabled
USE_COUNTING_SEMAPHORES | Disabled
QUEUE_REGISTRY_SIZE | 8
USE_APPLICATION_TASK_TAG | Disabled
ENABLE_BACKWARD_COMPATIBILITY | Enabled
USE_PORT_OPTIMISED_TASK_SELECTION | Enabled
USE_TICKLESS_IDLE | Disabled
USE_TASK_NOTIFICATIONS | Enabled
RECORD_STACK_HIGH_ADDRESS | Disabled

### Memory management settings:

Memory Allocation | Dynamic / Static
TOTAL_HEAP_SIZE | 15360
Memory Management scheme | heap_4

### Hook function related definitions:

USE_IDLE_HOOK | Disabled
USE_TICK_HOOK | Disabled
USE_MALLOC_FAILED_HOOK | Disabled
USE_DAEMON_TASK_STARTUP_HOOK | Disabled
CHECK_FOR_STACK_OVERFLOW | Disabled

### Run time and task stats gathering related definitions:

GENERATE_RUN_TIME_STATS | Disabled
USE_TRACE_FACILITY | Disabled
USE_STATS_FORMATTING_FUNCTIONS | Disabled

### Co-routine related definitions:

USE_CO_ROUTINES | Disabled
MAX_CO_ROUTINE_PRIORITIES | 2

### Software timer definitions:

USE_TIMERS

| Enabled *
TIMER_TASK_PRIORITY | 2
TIMER_QUEUE_LENGTH | 10
TIMER_TASK_STACK_DEPTH | 256

### Interrupt nesting behaviour configuration:

LIBRARY_LOWEST_INTERRUPT_PRIORITY | 15
LIBRARY_MAX_SYSCALL_INTERRUPT_PRIORITY | 5

### Added with 10.2.1 support:

MESSAGE_BUFFER_LENGTH_TYPE | size_t
USE_POSIX_ERRNO | Disabled

## 7.18.2. Include parameters:

### Include definitions:

vTaskPrioritySet | Enabled
uxTaskPriorityGet | Enabled
vTaskDelete | Enabled
vTaskCleanUpResources | Disabled
vTaskSuspend | Enabled
vTaskDelayUntil | Disabled
vTaskDelay | Enabled
xTaskGetSchedulerState | Enabled
xTaskResumeFromISR | Enabled
xQueueGetMutexHolder | Disabled
xSemaphoreGetMutexHolder | Disabled
pcTaskGetTaskName | Disabled
uxTaskGetStackHighWaterMark | Disabled
xTaskGetCurrentTaskHandle | Disabled
eTaskGetState | Disabled
xEventGroupSetBitFromISR | Disabled
xTimerPendFunctionCall | Disabled
xTaskAbortDelay | Disabled
xTaskGetHandle | Disabled
uxTaskGetStackHighWaterMark2 | Disabled

## 7.18.3. Advanced settings:

### Newlib settings (see parameter description first):

USE_NEWLIB_REENTRANT | Disabled

### Project settings (see parameter description first):

Use FW pack heap file | Enabled

### * User modified value

# 8. System Configuration

## 8.1. GPIO configuration

IP | Pin | Signal | GPIO mode | GPIO pull/up pull down | Max Speed | User Label
ADC1 | PC0 | ADC1_IN10 | Analog mode | No pull-up and no pull-down | n/a | JP9-THERM
| PC1 | ADC1_IN11 | Analog mode | No pull-up and no pull-down | n/a | JP8-THERM
| PC2 | ADC1_IN12 | Analog mode | No pull-up and no pull-down | n/a | JP10-THERM
| PC3 | ADC1_IN13 | Analog mode | No pull-up and no pull-down | n/a | JP11-THERM
| PA6 | ADC1_IN6 | Analog mode | No pull-up and no pull-down | n/a | JP34-ACtransfrmr
| PA7 | ADC1_IN7 | Analog mode | No pull-up and no pull-down | n/a | PWR12V+
| PC4 | ADC1_IN14 | Analog mode | No pull-up and no pull-down | n/a | JP17-SPARE
| PC5 | ADC1_IN15 | Analog mode | No pull-up and no pull-down | n/a | JP24-Pressure
| PB0 | ADC1_IN8 | Analog mode | No pull-up and no pull-down | n/a | STRING-PLUS
| PB1 | ADC1_IN9 | Analog mode | No pull-up and no pull-down | n/a | STRING-MINUS
ADC2 | PC1 | ADC2_IN11 | Analog mode | No pull-up and no pull-down | n/a | JP8-THERM
| PC2 | ADC2_IN12 | Analog mode | No pull-up and no pull-down | n/a | JP10-THERM
| PA6 | ADC2_IN6 | Analog mode | No pull-up and no pull-down | n/a | JP34-ACtransfrmr
| PC5 | ADC2_IN15 | Analog mode | No pull-up and no pull-down | n/a | JP24-Pressure
CAN1 | PB8 | CAN1_RX | Alternate Function Push Pull | No pull-up and no pull-down | Very High *
| PB9 | CAN1_TX | Alternate Function Push Pull | No pull-up and no pull-down | Very High *
CAN2 | PB5 | CAN2_RX | Alternate Function Push Pull | No pull-up and no pull-down | Very High *
| PB6 | CAN2_TX | Alternate Function Push Pull | No pull-up and no pull-down | Very High *
RCC | PC14-OSC32_IN | RCC_OSC32_IN | n/a | n/a | n/a
| PC15-OSC32_OU T | RCC_OSC32_O UT | n/a | n/a | n/a
| PH0-OSC_IN | RCC_OSC_IN | n/a | n/a | n/a
| PH1-OSC_OUT | RCC_OSC_OUT | n/a | n/a | n/a
RTC | PC13 | RTC_AF1 | n/a | n/a | n/a
SYS | PA13 | SYS_JTMS-SWDIO | n/a | n/a | n/a
| PA14 | SYS_JTCK-SWCLK | n/a | n/a | n/a
TIM1 | PA8 | TIM1_CH1 | Alternate Function Push Pull | No pull-up and no pull-down | Low | OC3

IP | Pin | Signal | GPIO mode | GPIO pull/up pull down | Max Speed | User Label
| PA9 | TIM1_CH2 | Alternate Function Push Pull | No pull-up and no pull-down | Low | OC1
| PA10 | TIM1_CH3 | Alternate Function Push Pull | No pull-up and no pull-down | Low | OC4
| PA11 | TIM1_CH4 | Alternate Function Push Pull | No pull-up and no pull-down | Low | OC2
TIM2 | PB2 | TIM2_CH4 | Alternate Function Push Pull | No pull-up and no pull-down | Low | HDR-OA3
| PB10 | TIM2_CH3 | Alternate Function Push Pull | No pull-up and no pull-down | Low
| PB3 | TIM2_CH2 | Alternate Function Push Pull | No pull-up and no pull-down | Low | JP21-FETSUB104
TIM3 | PC6 | TIM3_CH1 | Alternate Function Push Pull | No pull-up and no pull-down | Low | OB3
| PC7 | TIM3_CH2 | Alternate Function Push Pull | No pull-up and no pull-down | Low | OB1
| PC8 | TIM3_CH3 | Alternate Function Push Pull | No pull-up and no pull-down | Low | OB2
| PC9 | TIM3_CH4 | Alternate Function Push Pull | No pull-up and no pull-down | Low | OB4
TIM12 | PB14 | TIM12_CH1 | Alternate Function Push Pull | No pull-up and no pull-down | Low | OA4
| PB15 | TIM12_CH2 | Alternate Function Push Pull | No pull-up and no pull-down | Low | OA2
UART5 | PC12 | UART5_TX | Alternate Function Push Pull | No pull-up and no pull-down | Very High *
| PD2 | UART5_RX | Alternate Function Push Pull | No pull-up and no pull-down | Very High *
USART2 | PA2 | USART2_TX | Alternate Function Push Pull | No pull-up and no pull-down | Very High *
| PA3 | USART2_RX | Alternate Function Push Pull | No pull-up and no pull-down | Very High *
USART3 | PC10 | USART3_TX | Alternate Function Push Pull | No pull-up and no pull-down | Very High *
| PC11 | USART3_RX | Alternate Function Push Pull | No pull-up and no pull-down | Very High *
GPIO | PA5 | GPIO_Output | Output Push Pull | No pull-up and no pull-down | Low | M-RESET
| PB12 | GPIO_Output | Output Push Pull | No pull-up and no pull-down | Low | LED5-GRN
| PB13 | GPIO_Output | Output Push Pull | No pull-up and no pull-down | Low | LED6-RED
| PA12 | GPIO_Input | Input mode | No pull-up and no pull-down | n/a | Keyswsense
| PA15 | GPIO_EXTI15 | External Interrupt Mode with Rising edge trigger detection | Pull-up * | n/a | ACzeroxing
| PB4 | GPIO_Input | Input mode | No pull-up and no pull-down | n/a | JP14-IN

## 8.2. DMA configuration

DMA request | Stream | Direction | Priority
UART5_RX | DMA1_Stream0 | Peripheral To Memory | Low
USART2_TX | DMA1_Stream6 | Memory To Peripheral | Low
USART3_RX | DMA1_Stream1 | Peripheral To Memory | Low
USART3_TX | DMA1_Stream3 | Memory To Peripheral | Low
ADC1 | DMA2_Stream0 | Peripheral To Memory | Low
USART2_RX | DMA1_Stream5 | Peripheral To Memory | Low
ADC2 | DMA2_Stream2 | Peripheral To Memory | Low
MEMTOMEM | DMA2_Stream1 | Memory To Memory | Low

## UART5_RX: DMA1_Stream0 DMA request Settings:

Mode: | Circular *
Use fifo: | Disable
Peripheral Increment: | Disable
Memory Increment: | Enable *
Peripheral Data Width: | Byte
Memory Data Width: | Byte

## USART2_TX: DMA1_Stream6 DMA request Settings:

Mode: | Normal
Use fifo: | Disable
Peripheral Increment: | Disable
Memory Increment: | Enable *
Peripheral Data Width: | Byte
Memory Data Width: | Byte

## USART3_RX: DMA1_Stream1 DMA request Settings:

Mode: | Circular *
Use fifo: | Disable
Peripheral Increment: | Disable
Memory Increment: | Enable *
Peripheral Data Width: | Byte
Memory Data Width: | Byte

## USART3_TX: DMA1_Stream3 DMA request Settings:

Mode: | Normal
Use fifo: | Disable
Peripheral Increment: | Disable
Memory Increment: | Enable *
Peripheral Data Width: | Byte
Memory Data Width: | Byte

## ADC1: DMA2_Stream0 DMA request Settings:

Mode: | Circular *
Use fifo: | Disable
Peripheral Increment: | Disable
Memory Increment: | Enable *
Peripheral Data Width: | Half Word
Memory Data Width: | Half Word

## USART2_RX: DMA1_Stream5 DMA request Settings:

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

## ADC2: DMA2_Stream2 DMA request Settings:

Mode: | Circular *
Use fifo: | Disable
Peripheral Increment: | Disable
Memory Increment: | Enable *
Peripheral Data Width: | Half Word
Memory Data Width: | Half Word

## MEMTOMEM: DMA2_Stream1 DMA request Settings:

Mode: | Normal
Use fifo: | Enable *
FIFO Threshold: | Full
Src Memory Increment: | Enable *
Dst Memormy Increment: | Enable *
Src Memory Data Width: | Word *
Dst Memormy Data Width: | Word *
Src Memory Burst Size: | Single
Dst Memormy Burst Size: | Single

## 8.3. NVIC configuration

## 8.3.1. NVIC

Interrupt Table | Enable | Preenmption Priority | SubPriority
Non maskable interrupt | true | 0 | 0
Hard fault interrupt | true | 0 | 0
Memory management fault | true | 0 | 0
Pre-fetch fault, memory access fault | true | 0 | 0
Undefined instruction or illegal state | true | 0 | 0
System service call via SWI instruction | true | 0 | 0
Debug monitor | true | 0 | 0
Pendable request for system service | true | 15 | 0
System tick timer | true | 15 | 0
DMA1 stream0 global interrupt | true | 5 | 0
DMA1 stream1 global interrupt | true | 5 | 0
DMA1 stream3 global interrupt | true | 5 | 0
DMA1 stream5 global interrupt | true | 5 | 0
DMA1 stream6 global interrupt | true | 5 | 0
CAN1 TX interrupt | true | 5 | 0
CAN1 RX0 interrupt | true | 5 | 0
CAN1 RX1 interrupt | true | 5 | 0
TIM1 break interrupt and TIM9 global interrupt | true | 8 | 0
USART2 global interrupt | true | 5 | 0
USART3 global interrupt | true | 5 | 0
EXTI line[15:10] interrupts | true | 2 | 0
TIM8 update interrupt and TIM13 global interrupt | true | 8 | 0
TIM8 trigger and commutation interrupts and TIM14 global interrupt | true | 15 | 0
TIM5 global interrupt | true | 8 | 0
UART5 global interrupt | true | 5 | 0
DMA2 stream0 global interrupt | true | 5 | 0
DMA2 stream1 global interrupt | true | 5 | 0
DMA2 stream2 global interrupt | true | 5 | 0
CAN2 TX interrupt | true | 5 | 0
CAN2 RX0 interrupt | true | 5 | 0
CAN2 RX1 interrupt | true | 5 | 0
PVD interrupt through EXTI line 16 | | unused
RTC wake-up interrupt through EXTI line 22 | | unused
Flash global interrupt | | unused
RCC global interrupt | | unused
ADC1, ADC2 and ADC3 interrupts | | unused

Interrupt Table | Enable | Preenmption Priority | SubPriority
CAN1 SCE interrupt | unused
TIM1 update interrupt and TIM10 global interrupt | unused
TIM1 trigger and commutation interrupts and TIM11 global interrupt | unused
TIM1 capture compare interrupt | unused
TIM2 global interrupt | unused
TIM3 global interrupt | unused
TIM8 break interrupt and TIM12 global interrupt | unused
CAN2 SCE interrupt | unused
FPU global interrupt | unused

## 8.3.2. NVIC Code generation

Enabled interrupt Table | Select for init sequence ordering | Generate IRQ handler | Call HAL handler
Non maskable interrupt | false | true | false
Hard fault interrupt | false | true | false
Memory management fault | false | true | false
Pre-fetch fault, memory access fault | false | true | false
Undefined instruction or illegal state | false | true | false
System service call via SWI instruction | false | false | false
Debug monitor | false | true | false
Pendable request for system service | false | false | false
System tick timer | false | false | true
DMA1 stream0 global interrupt | false | true | true
DMA1 stream1 global interrupt | false | true | true
DMA1 stream3 global interrupt | false | true | true
DMA1 stream5 global interrupt | false | true | true
DMA1 stream6 global interrupt | false | true | true
CAN1 TX interrupt | false | true | true
CAN1 RX0 interrupt | false | true | true
CAN1 RX1 interrupt | false | true | true
TIM1 break interrupt and TIM9 global interrupt | false | true | true
USART2 global interrupt | false | true | true
USART3 global interrupt | false | true | true
EXTI line[15:10] interrupts | false | true | true
TIM8 update interrupt and TIM13 global interrupt | false | true | true
TIM8 trigger and commutation interrupts and TIM14 global interrupt | false | true | true
TIM5 global interrupt | false | true | true

Enabled interrupt Table | Select for init sequence ordering | Generate IRQ handler | Call HAL handler
UART5 global interrupt | false | true | true
DMA2 stream0 global interrupt | false | true | true
DMA2 stream1 global interrupt | false | true | true
DMA2 stream2 global interrupt | false | true | true
CAN2 TX interrupt | false | true | true
CAN2 RX0 interrupt | false | true | true
CAN2 RX1 interrupt | false | true | true

### * User modified value

# 9. System Views

## 9.1. Category view 9.1.1. Current

# 10. Docs & Resources

Type | Link
Datasheet | http://www.st.com/resource/en/datasheet/DM00141306.pdf
Reference manual | http://www.st.com/resource/en/reference_manual/DM00135183.pdf
Programming manual | http://www.st.com/resource/en/programming_manual/DM00046982.pdf
Errata sheet | http://www.st.com/resource/en/errata_sheet/DM00155929.pdf
Application note | http://www.st.com/resource/en/application_note/CD00167594.pdf
Application note | http://www.st.com/resource/en/application_note/CD00211314.pdf
Application note | http://www.st.com/resource/en/application_note/CD00249778.pdf
Application note | http://www.st.com/resource/en/application_note/CD00259245.pdf
Application note | http://www.st.com/resource/en/application_note/CD00264321.pdf
Application note | http://www.st.com/resource/en/application_note/CD00264342.pdf
Application note | http://www.st.com/resource/en/application_note/CD00264379.pdf
Application note | http://www.st.com/resource/en/application_note/DM00024853.pdf
Application note | http://www.st.com/resource/en/application_note/DM00040802.pdf
Application note | http://www.st.com/resource/en/application_note/DM00040808.pdf
Application note | http://www.st.com/resource/en/application_note/DM00042534.pdf
Application note | http://www.st.com/resource/en/application_note/DM00046011.pdf
Application note | http://www.st.com/resource/en/application_note/DM00072315.pdf
Application note | http://www.st.com/resource/en/application_note/DM00073742.pdf
Application note | http://www.st.com/resource/en/application_note/DM00073853.pdf
Application note | http://www.st.com/resource/en/application_note/DM00080497.pdf
Application note | http://www.st.com/resource/en/application_note/DM00081379.pdf
Application note | http://www.st.com/resource/en/application_note/DM00115714.pdf
Application note | http://www.st.com/resource/en/application_note/DM00129215.pdf
Application note | http://www.st.com/resource/en/application_note/DM00154959.pdf
Application note | http://www.st.com/resource/en/application_note/DM00160482.pdf

Application note | http://www.st.com/resource/en/application_note/DM00161778.pdf
Application note | http://www.st.com/resource/en/application_note/DM00213525.pdf
Application note | http://www.st.com/resource/en/application_note/DM00220769.pdf
Application note | http://www.st.com/resource/en/application_note/DM00226326.pdf
Application note | http://www.st.com/resource/en/application_note/DM00227538.pdf
Application note | http://www.st.com/resource/en/application_note/DM00236305.pdf
Application note | http://www.st.com/resource/en/application_note/DM00257177.pdf
Application note | http://www.st.com/resource/en/application_note/DM00272912.pdf
Application note | http://www.st.com/resource/en/application_note/DM00281138.pdf
Application note | http://www.st.com/resource/en/application_note/DM00296349.pdf
Application note | http://www.st.com/resource/en/application_note/DM00315319.pdf
Application note | http://www.st.com/resource/en/application_note/DM00327191.pdf
Application note | http://www.st.com/resource/en/application_note/DM00354244.pdf
Application note | http://www.st.com/resource/en/application_note/DM00373474.pdf
Application note | http://www.st.com/resource/en/application_note/DM00380469.pdf
Application note | http://www.st.com/resource/en/application_note/DM00395696.pdf
Application note | http://www.st.com/resource/en/application_note/DM00431633.pdf
Application note | http://www.st.com/resource/en/application_note/DM00493651.pdf
Application note | http://www.st.com/resource/en/application_note/DM00536349.pdf
Application note | http://www.st.com/resource/en/application_note/DM00725181.pdf

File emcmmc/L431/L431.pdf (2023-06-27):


27/06/2023

## L431 Project Configuration Report

# 1. Description

## 1.1. Project

Project Name | L431
Board Name | custom
Generated with: | STM32CubeMX 6.3.0
Date | 06/27/2023

## 1.2. MCU

MCU Series | STM32L4
MCU Line | STM32L4x1
MCU name | STM32L431RCTx
MCU Package | LQFP64
MCU Pin number | 64

## 1.3. Core(s) information

Core(s) | Arm Cortex-M4

# 2. Pinout Configuration

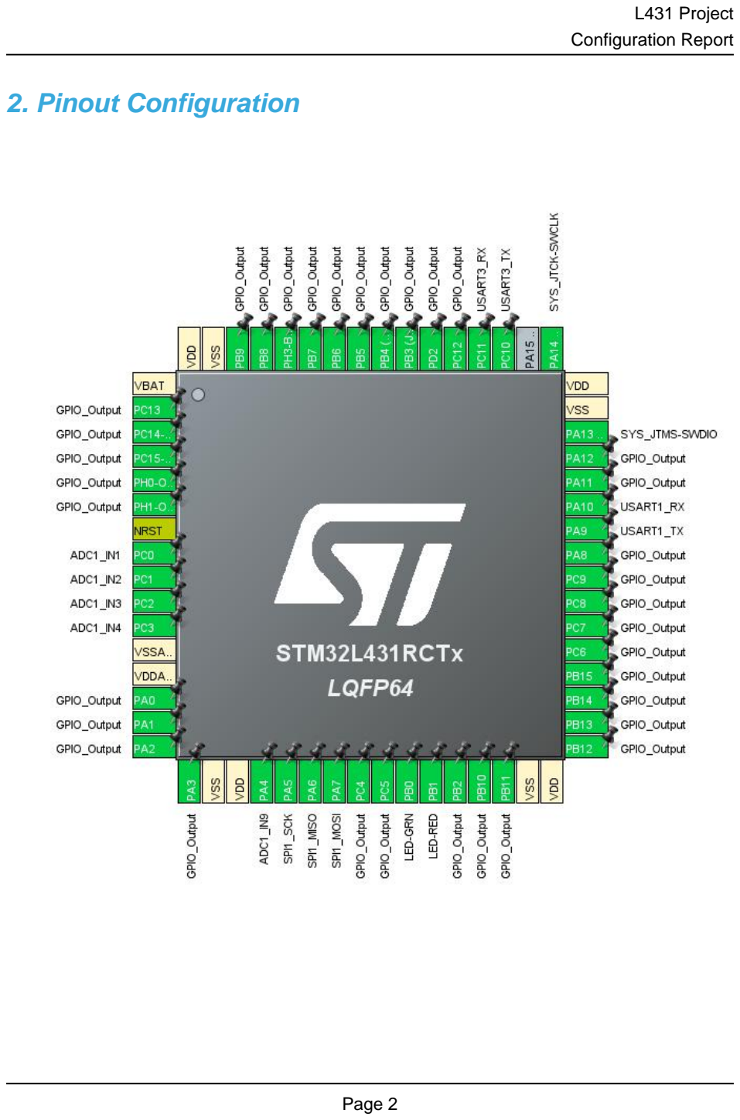
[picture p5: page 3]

# 3. Pins Configuration

Pin Number LQFP64 | Pin Name (function after reset) | Pin Type | Alternate Function(s) | Label
1 | VBAT | Power
2 | PC13 * | I/O | GPIO_Output
3 | PC14-OSC32_IN (PC14) * | I/O | GPIO_Output
4 | PC15-OSC32_OUT (PC15) * | I/O | GPIO_Output
5 | PH0-OSC_IN (PH0) * | I/O | GPIO_Output
6 | PH1-OSC_OUT (PH1) * | I/O | GPIO_Output
7 | NRST | Reset
8 | PC0 | I/O | ADC1_IN1
9 | PC1 | I/O | ADC1_IN2
10 | PC2 | I/O | ADC1_IN3
11 | PC3 | I/O | ADC1_IN4
12 | VSSA/VREF- | Power
13 | VDDA/VREF+ | Power
14 | PA0 * | I/O | GPIO_Output
15 | PA1 * | I/O | GPIO_Output
16 | PA2 * | I/O | GPIO_Output
17 | PA3 * | I/O | GPIO_Output
18 | VSS | Power
19 | VDD | Power
20 | PA4 | I/O | ADC1_IN9
21 | PA5 | I/O | SPI1_SCK
22 | PA6 | I/O | SPI1_MISO
23 | PA7 | I/O | SPI1_MOSI
24 | PC4 * | I/O | GPIO_Output
25 | PC5 * | I/O | GPIO_Output
26 | PB0 * | I/O | GPIO_Output | LED-GRN
27 | PB1 * | I/O | GPIO_Output | LED-RED
28 | PB2 * | I/O | GPIO_Output
29 | PB10 * | I/O | GPIO_Output
30 | PB11 * | I/O | GPIO_Output
31 | VSS | Power
32 | VDD | Power
33 | PB12 * | I/O | GPIO_Output
34 | PB13 * | I/O | GPIO_Output
35 | PB14 * | I/O | GPIO_Output

Pin Number LQFP64 | Pin Name (function after reset) | Pin Type | Alternate Function(s) | Label
36 | PB15 * | I/O | GPIO_Output
37 | PC6 * | I/O | GPIO_Output
38 | PC7 * | I/O | GPIO_Output
39 | PC8 * | I/O | GPIO_Output
40 | PC9 * | I/O | GPIO_Output
41 | PA8 * | I/O | GPIO_Output
42 | PA9 | I/O | USART1_TX
43 | PA10 | I/O | USART1_RX
44 | PA11 * | I/O | GPIO_Output
45 | PA12 * | I/O | GPIO_Output
46 | PA13 (JTMS-SWDIO) | I/O | SYS_JTMS-SWDIO
47 | VSS | Power
48 | VDD | Power
49 | PA14 (JTCK-SWCLK) | I/O | SYS_JTCK-SWCLK
51 | PC10 | I/O | USART3_TX
52 | PC11 | I/O | USART3_RX
53 | PC12 * | I/O | GPIO_Output
54 | PD2 * | I/O | GPIO_Output
55 | PB3 (JTDO-TRACESWO) * | I/O | GPIO_Output
56 | PB4 (NJTRST) * | I/O | GPIO_Output
57 | PB5 * | I/O | GPIO_Output
58 | PB6 * | I/O | GPIO_Output
59 | PB7 * | I/O | GPIO_Output
60 | PH3-BOOT0 * | I/O | GPIO_Output
61 | PB8 * | I/O | GPIO_Output
62 | PB9 * | I/O | GPIO_Output
63 | VSS | Power
64 | VDD | Power

## * The pin is affected with an I/O function

# 4. Clock Tree Configuration

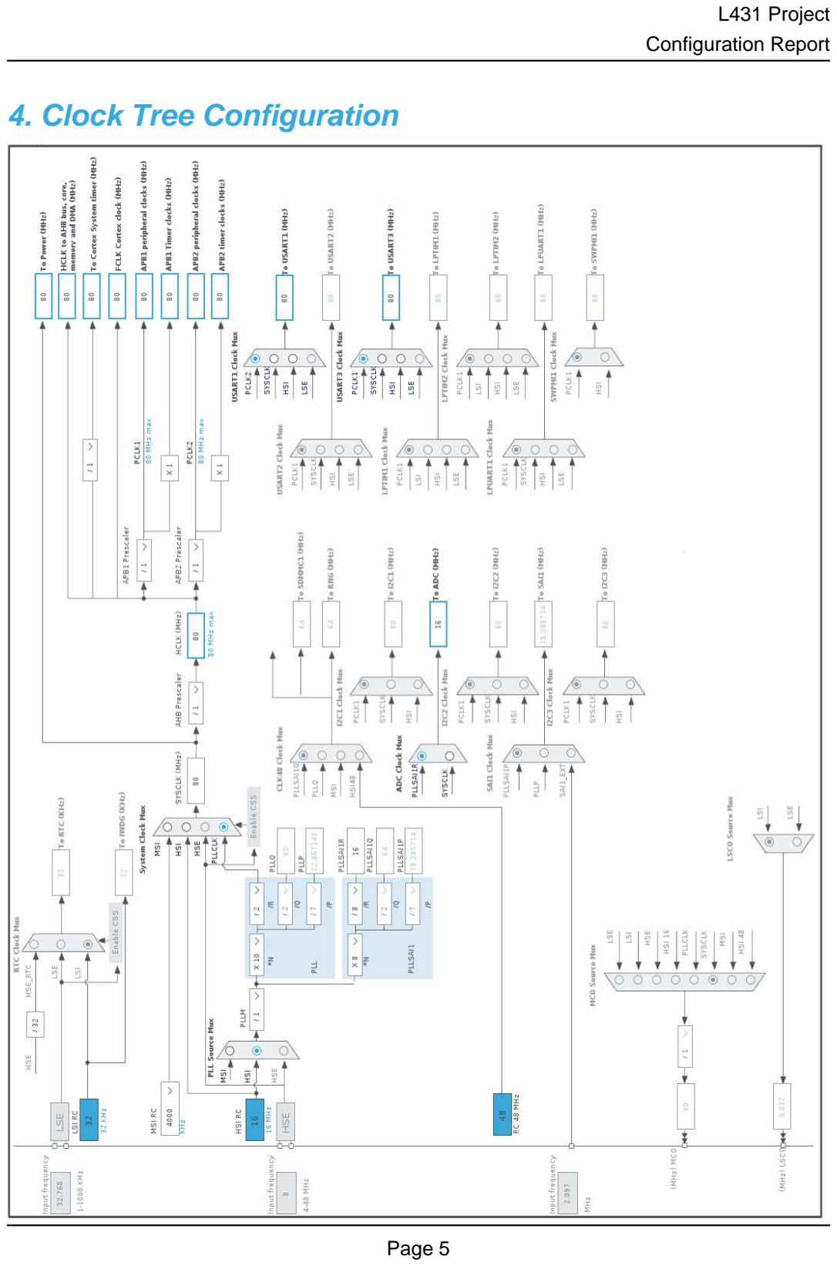
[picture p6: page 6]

# 5. Software Project

## 5.1. Project Settings

Name | Value
Project Name | L431
Project Folder | /home/deh/GliderWinchItems/bmsmot/emcmmc/L431
Toolchain / IDE | Makefile
Firmware Package Name and Version | STM32Cube FW_L4 V1.17.2
Application Structure | Advanced
Generate Under Root | No
Do not generate the main() | No
Minimum Heap Size | 0x200
Minimum Stack Size | 0x400

## 5.2. Code Generation Settings

Name | Value
STM32Cube MCU packages and embedded software | Copy all used libraries into the project folder
Generate peripheral initialization as a pair of '.c/.h' files | No
Backup previously generated files when re-generating | No
Keep User Code when re-generating | Yes
Delete previously generated files when not re-generated | Yes
Set all free pins as analog (to optimize the power consumption) | No
Enable Full Assert | No

## 5.3. Advanced Settings - Generated Function Calls

Rank | Function Name | Peripheral Instance Name
1 | SystemClock_Config | RCC
2 | MX_GPIO_Init | GPIO
3 | MX_DMA_Init | DMA
4 | MX_USART1_UART_Init | USART1
5 | MX_USART3_UART_Init | USART3
6 | MX_ADC1_Init | ADC1
7 | MX_SPI1_Init | SPI1

# 6. Power Consumption Calculator report

## 6.1. Microcontroller Selection

Series | STM32L4
Line | STM32L4x1
MCU | STM32L431RCTx
Datasheet | DS11453_Rev1

## 6.2. Parameter Selection

Temperature | 25
Vdd | 3.0

## 6.3. Battery Selection

Battery | Li-SOCL2(A3400)
Capacity | 3400.0 mAh
Self Discharge | 0.08 %/month
Nominal Voltage | 3.6 V
Max Cont Current | 100.0 mA
Max Pulse Current | 200.0 mA
Cells in series | 1
Cells in parallel | 1

## 6.4. Sequence

Step | Step1 | Step2
Mode | RUN | STOP2
Vdd | 3.0 | 3.0
Voltage Source | Battery | Battery
Range | Range1-High | NoRange
Fetch Type | SRAM2 | n/a
CPU Frequency | 80 MHz | 0 Hz
Clock Configuration | HSE BYP PLL | ALL CLOCKS OFF
Clock Source Frequency | 4 MHz | 0 Hz

### Peripherals

Additional Cons. | 0 mA | 0 mA
Average Current | 8.71 mA | 1.06 µA
Duration | 0.1 ms | 0.9 ms
DMIPS | 100.0 | 0.0
Ta Max | 103.82 | 105
Category | In DS Table | In DS Table

## 6.5. Results

Sequence Time | 1 ms | Average Current | 871.95 µA
Battery Life | 5 months, 9 days, 16 hours | Average DMIPS | 100.0 DMIPS

## 6.6. Chart

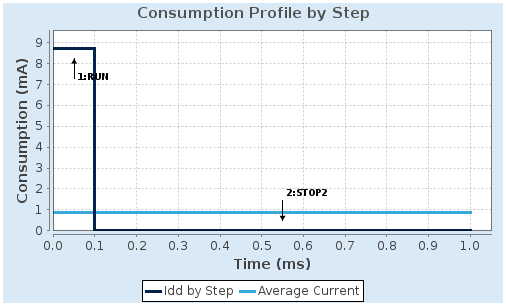
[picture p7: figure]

# 7. Peripherals and Middlewares Configuration

## 7.1. ADC1 IN1: IN1 Single-ended IN2: IN2 Single-ended IN3: IN3 Single-ended IN4: IN4 Single-ended IN9: IN9 Single-ended IN17: Temperature Sensor Channel mode: Vrefint Channel

## 7.1.1. Parameter Settings:

### ADC_Settings:

Clock Prescaler | Asynchronous clock mode divided by 1
Resolution | ADC 12-bit resolution
Data Alignment | Right alignment
Scan Conversion Mode | Enabled
Continuous Conversion Mode | Enabled *
Discontinuous Conversion Mode | Disabled
DMA Continuous Requests | Enabled *
End Of Conversion Selection | End of single conversion
Overrun behaviour | Overrun data preserved
Low Power Auto Wait | Disabled

### ADC_Regular_ConversionMode:

Enable Regular Conversions | Enable
Enable Regular Oversampling | Disable
Number Of Conversion | 7 *
External Trigger Conversion Source | Regular Conversion launched by software
External Trigger Conversion Edge | None
Rank | 1
Channel | Channel 1
Sampling Time | 47.5 Cycles *
Offset Number | No offset
Rank | 2 *
Channel | Channel 2 *
Sampling Time | 47.5 Cycles *
Offset Number | No offset
Rank | 3 *
Channel | Channel 3 *

Sampling Time | 47.5 Cycles *
Offset Number | No offset
Rank | 4 *
Channel | Channel 4 *
Sampling Time | 47.5 Cycles *
Offset Number | No offset
Rank | 5 *
Channel | Channel 9 *
Sampling Time | 47.5 Cycles *
Offset Number | No offset
Rank | 6 *
Channel | Channel Vrefint *
Sampling Time | 247.5 Cycles *
Offset Number | No offset
Rank | 7 *
Channel | Channel Temperature Sensor *
Sampling Time | 247.5 Cycles *
Offset Number | No offset

### ADC_Injected_ConversionMode:

Enable Injected Conversions | Disable

### Analog Watchdog 1:

Enable Analog WatchDog1 Mode | false

### Analog Watchdog 2:

Enable Analog WatchDog2 Mode | false

### Analog Watchdog 3:

Enable Analog WatchDog3 Mode | false

## 7.2. RCC

## 7.2.1. Parameter Settings:

### System Parameters:

VDD voltage (V) | 3.3
Instruction Cache | Enabled
Prefetch Buffer | Disabled
Data Cache | Enabled
Flash Latency(WS) | 4 WS (5 CPU cycle)

### RCC Parameters:

HSI Calibration Value | 16
MSI Calibration Value | 0
MSI Auto Calibration | Disabled
HSE Startup Timout Value (ms) | 100
LSE Startup Timout Value (ms) | 5000

### Power Parameters:

Power Regulator Voltage Scale | Power Regulator Voltage Scale 1

## 7.3. SPI1 Mode: Full-Duplex Master

## 7.3.1. Parameter Settings:

### Basic Parameters:

Frame Format | Motorola
Data Size | 4 Bits
First Bit | MSB First

### Clock Parameters:

Prescaler (for Baud Rate) | 2
Baud Rate | 40.0 MBits/s *
Clock Polarity (CPOL) | Low
Clock Phase (CPHA) | 1 Edge

### Advanced Parameters:

CRC Calculation | Disabled
NSSP Mode | Enabled
NSS Signal Type | Software

## 7.4. SYS Debug: Serial Wire Timebase Source: TIM16

## 7.5. USART1 Mode: Asynchronous

## 7.5.1. Parameter Settings:

### Basic Parameters:

Baud Rate | 115200
Word Length | 8 Bits (including Parity)

Parity | None
Stop Bits | 1

### Advanced Parameters:

Data Direction | Receive and Transmit
Over Sampling | 16 Samples
Single Sample | Disable

### Advanced Features:

Auto Baudrate | Disable
TX Pin Active Level Inversion | Disable
RX Pin Active Level Inversion | Disable
Data Inversion | Disable
TX and RX Pins Swapping | Disable
Overrun | Enable
DMA on RX Error | Enable
MSB First | Disable

## 7.6. USART3 Mode: Asynchronous

## 7.6.1. Parameter Settings:

### Basic Parameters:

Baud Rate | 115200
Word Length | 8 Bits (including Parity)
Parity | None
Stop Bits | 1

### Advanced Parameters:

Data Direction | Receive and Transmit
Over Sampling | 16 Samples
Single Sample | Disable

### Advanced Features:

Auto Baudrate | Disable
TX Pin Active Level Inversion | Disable
RX Pin Active Level Inversion | Disable
Data Inversion | Disable
TX and RX Pins Swapping | Disable
Overrun | Enable
DMA on RX Error | Enable
MSB First | Disable

## 7.7. FREERTOS Interface: CMSIS_V1

## 7.7.1. Config parameters:

### API:

FreeRTOS API | CMSIS v1

### Versions:

FreeRTOS version | 10.3.1
CMSIS-RTOS version | 1.02

### MPU/FPU:

ENABLE_MPU | Disabled
ENABLE_FPU | Disabled

### Kernel settings:

USE_PREEMPTION | Enabled
CPU_CLOCK_HZ | SystemCoreClock
TICK_RATE_HZ | 1000
MAX_PRIORITIES | 7
MINIMAL_STACK_SIZE | 128
MAX_TASK_NAME_LEN | 16
USE_16_BIT_TICKS | Disabled
IDLE_SHOULD_YIELD | Enabled
USE_MUTEXES | Enabled
USE_RECURSIVE_MUTEXES | Disabled
USE_COUNTING_SEMAPHORES | Disabled
QUEUE_REGISTRY_SIZE | 8
USE_APPLICATION_TASK_TAG | Disabled
ENABLE_BACKWARD_COMPATIBILITY | Enabled
USE_PORT_OPTIMISED_TASK_SELECTION | Enabled
USE_TICKLESS_IDLE | Disabled
USE_TASK_NOTIFICATIONS | Enabled
RECORD_STACK_HIGH_ADDRESS | Disabled

### Memory management settings:

Memory Allocation | Dynamic / Static
TOTAL_HEAP_SIZE | 8000 *
Memory Management scheme | heap_4

### Hook function related definitions:

USE_IDLE_HOOK | Disabled
USE_TICK_HOOK | Disabled

USE_MALLOC_FAILED_HOOK | Disabled
USE_DAEMON_TASK_STARTUP_HOOK | Disabled
CHECK_FOR_STACK_OVERFLOW | Disabled

### Run time and task stats gathering related definitions:

GENERATE_RUN_TIME_STATS | Disabled
USE_TRACE_FACILITY | Disabled
USE_STATS_FORMATTING_FUNCTIONS | Disabled

### Co-routine related definitions:

USE_CO_ROUTINES | Disabled
MAX_CO_ROUTINE_PRIORITIES | 2

### Software timer definitions:

USE_TIMERS | Disabled

### Interrupt nesting behaviour configuration:

LIBRARY_LOWEST_INTERRUPT_PRIORITY | 15
LIBRARY_MAX_SYSCALL_INTERRUPT_PRIORITY | 5

### Added with 10.2.1 support:

MESSAGE_BUFFER_LENGTH_TYPE | size_t
USE_POSIX_ERRNO | Disabled

## 7.7.2. Include parameters:

### Include definitions:

vTaskPrioritySet | Enabled
uxTaskPriorityGet | Enabled
vTaskDelete | Enabled
vTaskCleanUpResources | Disabled
vTaskSuspend | Enabled
vTaskDelayUntil | Disabled
vTaskDelay | Enabled
xTaskGetSchedulerState | Enabled
xTaskResumeFromISR | Enabled
xQueueGetMutexHolder | Disabled
xSemaphoreGetMutexHolder | Disabled
pcTaskGetTaskName | Disabled
uxTaskGetStackHighWaterMark | Disabled
xTaskGetCurrentTaskHandle | Disabled
eTaskGetState | Disabled
xEventGroupSetBitFromISR | Disabled
xTimerPendFunctionCall | Disabled
xTaskAbortDelay | Disabled
xTaskGetHandle | Disabled

uxTaskGetStackHighWaterMark2 | Disabled

## 7.7.3. Advanced settings:

### Newlib settings (see parameter description first):

USE_NEWLIB_REENTRANT | Disabled

### Project settings (see parameter description first):

Use FW pack heap file | Enabled

### * User modified value

# 8. System Configuration

## 8.1. GPIO configuration

IP | Pin | Signal | GPIO mode | GPIO pull/up pull down

## Max Speed

## User Label

ADC1 | PC0 | ADC1_IN1 | Analog mode for ADC conversion | No pull-up and no pull-down | n/a
| PC1 | ADC1_IN2 | Analog mode for ADC conversion | No pull-up and no pull-down | n/a
| PC2 | ADC1_IN3 | Analog mode for ADC conversion | No pull-up and no pull-down | n/a
| PC3 | ADC1_IN4 | Analog mode for ADC conversion | No pull-up and no pull-down | n/a
| PA4 | ADC1_IN9 | Analog mode for ADC conversion | No pull-up and no pull-down | n/a
SPI1 | PA5 | SPI1_SCK | Alternate Function Push Pull | No pull-up and no pull-down | Very High
*
| PA6 | SPI1_MISO | Alternate Function Push Pull | No pull-up and no pull-down | Very High
*
| PA7 | SPI1_MOSI | Alternate Function Push Pull | No pull-up and no pull-down | Very High
*
SYS | PA13 (JTMS- SWDIO) | SYS_JTMS- SWDIO | n/a | n/a | n/a

PA14 (JTCK-SWCLK)

SYS_JTCK-SWCLK

| | | n/a | n/a | n/a
USART1 | PA9 | USART1_TX | Alternate Function Push Pull | No pull-up and no pull-down | Very High
*
| PA10 | USART1_RX | Alternate Function Push Pull | No pull-up and no pull-down | Very High
*
USART3 | PC10 | USART3_TX | Alternate Function Push Pull | No pull-up and no pull-down | Very High
*
| PC11 | USART3_RX | Alternate Function Push Pull | No pull-up and no pull-down | Very High
*
GPIO | PC13 | GPIO_Output | Output Push Pull | No pull-up and no pull-down | Low
| PC14- OSC32_IN (PC14) | GPIO_Output | Output Push Pull | No pull-up and no pull-down | Low

PC15-
OSC32_OU
T (PC15)
GPIO_Output | Output Push Pull | No pull-up and no pull-down | Low
PH0- | GPIO_Output | Output Push Pull | No pull-up and no pull-down | Low

IP | Pin | Signal | GPIO mode | GPIO pull/up pull down | Max Speed | User Label
| OSC_IN (PH0)
| PH1-OSC_OUT (PH1) | GPIO_Output | Output Push Pull | No pull-up and no pull-down | Low
| PA0 | GPIO_Output | Output Push Pull | No pull-up and no pull-down | Low
| PA1 | GPIO_Output | Output Push Pull | No pull-up and no pull-down | Low
| PA2 | GPIO_Output | Output Push Pull | No pull-up and no pull-down | Low
| PA3 | GPIO_Output | Output Push Pull | No pull-up and no pull-down | Low
| PC4 | GPIO_Output | Output Push Pull | No pull-up and no pull-down | Low
| PC5 | GPIO_Output | Output Push Pull | No pull-up and no pull-down | Low
| PB0 | GPIO_Output | Output Open Drain * | No pull-up and no pull-down | Low | LED-GRN
| PB1 | GPIO_Output | Output Open Drain * | No pull-up and no pull-down | Low | LED-RED
| PB2 | GPIO_Output | Output Push Pull | No pull-up and no pull-down | Low
| PB10 | GPIO_Output | Output Push Pull | No pull-up and no pull-down | Low
| PB11 | GPIO_Output | Output Push Pull | No pull-up and no pull-down | Low
| PB12 | GPIO_Output | Output Push Pull | No pull-up and no pull-down | Low
| PB13 | GPIO_Output | Output Push Pull | No pull-up and no pull-down | Low
| PB14 | GPIO_Output | Output Push Pull | No pull-up and no pull-down | Low
| PB15 | GPIO_Output | Output Push Pull | No pull-up and no pull-down | Low
| PC6 | GPIO_Output | Output Push Pull | No pull-up and no pull-down | Low
| PC7 | GPIO_Output | Output Push Pull | No pull-up and no pull-down | Low
| PC8 | GPIO_Output | Output Push Pull | No pull-up and no pull-down | Low
| PC9 | GPIO_Output | Output Push Pull | No pull-up and no pull-down | Low
| PA8 | GPIO_Output | Output Push Pull | No pull-up and no pull-down | Low
| PA11 | GPIO_Output | Output Push Pull | No pull-up and no pull-down | Low
| PA12 | GPIO_Output | Output Push Pull | No pull-up and no pull-down | Low
| PC12 | GPIO_Output | Output Push Pull | No pull-up and no pull-down | Low
| PD2 | GPIO_Output | Output Push Pull | No pull-up and no pull-down | Low
| PB3 (JTDO-TRACESWO ) | GPIO_Output | Output Push Pull | No pull-up and no pull-down | Low
| PB4 (NJTRST) | GPIO_Output | Output Push Pull | No pull-up and no pull-down | Low
| PB5 | GPIO_Output | Output Push Pull | No pull-up and no pull-down | Low
| PB6 | GPIO_Output | Output Push Pull | No pull-up and no pull-down | Low
| PB7 | GPIO_Output | Output Push Pull | No pull-up and no pull-down | Low
| PH3-BOOT0 | GPIO_Output | Output Push Pull | No pull-up and no pull-down | Low
| PB8 | GPIO_Output | Output Push Pull | No pull-up and no pull-down | Low
| PB9 | GPIO_Output | Output Push Pull | No pull-up and no pull-down | Low

## 8.2. DMA configuration

DMA request | Stream | Direction | Priority
USART1_RX | DMA1_Channel5 | Peripheral To Memory | Low
USART1_TX | DMA1_Channel4 | Memory To Peripheral | Low
USART3_RX | DMA1_Channel3 | Peripheral To Memory | Low
USART3_TX | DMA1_Channel2 | Memory To Peripheral | Low
ADC1 | DMA1_Channel1 | Peripheral To Memory | Low

## USART1_RX: DMA1_Channel5 DMA request Settings:

Mode: | Normal
Peripheral Increment: | Disable
Memory Increment: | Enable *
Peripheral Data Width: | Byte
Memory Data Width: | Byte

## USART1_TX: DMA1_Channel4 DMA request Settings:

Mode: | Normal
Peripheral Increment: | Disable
Memory Increment: | Enable *
Peripheral Data Width: | Byte
Memory Data Width: | Byte

## USART3_RX: DMA1_Channel3 DMA request Settings:

Mode: | Normal
Peripheral Increment: | Disable
Memory Increment: | Enable *
Peripheral Data Width: | Byte
Memory Data Width: | Byte

## USART3_TX: DMA1_Channel2 DMA request Settings:

Mode: | Normal
Peripheral Increment: | Disable
Memory Increment: | Enable *
Peripheral Data Width: | Byte

Memory Data Width: Byte

## ADC1: DMA1_Channel1 DMA request Settings:

Mode: | Normal
Peripheral Increment: | Disable
Memory Increment: | Enable *
Peripheral Data Width: | Half Word
Memory Data Width: | Half Word

## 8.3. NVIC configuration

## 8.3.1. NVIC

Interrupt Table | Enable | Preenmption Priority | SubPriority
Non maskable interrupt | true | 0 | 0
Hard fault interrupt | true | 0 | 0
Memory management fault | true | 0 | 0
Prefetch fault, memory access fault | true | 0 | 0
Undefined instruction or illegal state | true | 0 | 0
System service call via SWI instruction | true | 0 | 0
Debug monitor | true | 0 | 0
Pendable request for system service | true | 15 | 0
System tick timer | true | 15 | 0
DMA1 channel1 global interrupt | true | 5 | 0
DMA1 channel2 global interrupt | true | 5 | 0
DMA1 channel3 global interrupt | true | 5 | 0
DMA1 channel4 global interrupt | true | 5 | 0
DMA1 channel5 global interrupt | true | 5 | 0
TIM1 update interrupt and TIM16 global interrupt | true | 15 | 0
USART1 global interrupt | true | 5 | 0
USART3 global interrupt | true | 5 | 0
PVD/PVM1/PVM2/PVM3/PVM4 interrupts through EXTI lines 16/35/36/37/38 | | unused
Flash global interrupt | | unused
RCC global interrupt | | unused
ADC1 global interrupt | | unused
SPI1 global interrupt | | unused
FPU global interrupt | | unused

## 8.3.2. NVIC Code generation

## Enabled interrupt Table Select for init sequence ordering

| | Generate IRQ
| | handler | Call HAL handler
Non maskable interrupt | false | true | false
Hard fault interrupt | false | true | false
Memory management fault | false | true | false
Prefetch fault, memory access fault | false | true | false
Undefined instruction or illegal state | false | true | false
System service call via SWI instruction | false | false | false
Debug monitor | false | true | false
Pendable request for system service | false | false | false

Enabled interrupt Table | Select for init sequence ordering | Generate IRQ handler | Call HAL handler
System tick timer | false | false | true
DMA1 channel1 global interrupt | false | true | true
DMA1 channel2 global interrupt | false | true | true
DMA1 channel3 global interrupt | false | true | true
DMA1 channel4 global interrupt | false | true | true
DMA1 channel5 global interrupt | false | true | true
TIM1 update interrupt and TIM16 global interrupt | false | true | true
USART1 global interrupt | false | true | true
USART3 global interrupt | false | true | true

### * User modified value

# 9. System Views

## 9.1. Category view 9.1.1. Current

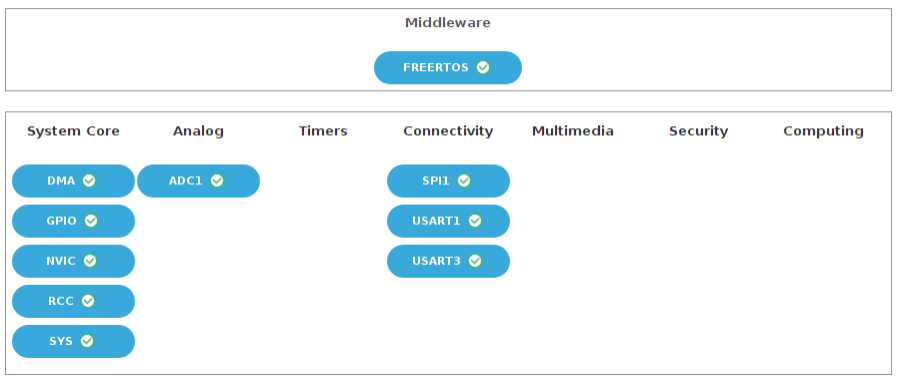
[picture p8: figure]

# 10. Docs & Resources

Type | Link
Datasheet | http://www.st.com/resource/en/datasheet/DM00257211.pdf
Reference manual | http://www.st.com/resource/en/reference_manual/DM00151940.pdf
Programming manual | http://www.st.com/resource/en/programming_manual/DM00046982.pdf
Errata sheet | http://www.st.com/resource/en/errata_sheet/DM00218224.pdf
Application note | http://www.st.com/resource/en/application_note/CD00160362.pdf
Application note | http://www.st.com/resource/en/application_note/CD00167594.pdf
Application note | http://www.st.com/resource/en/application_note/CD00211314.pdf
Application note | http://www.st.com/resource/en/application_note/CD00259245.pdf
Application note | http://www.st.com/resource/en/application_note/CD00264321.pdf
Application note | http://www.st.com/resource/en/application_note/CD00264342.pdf
Application note | http://www.st.com/resource/en/application_note/CD00264379.pdf
Application note | http://www.st.com/resource/en/application_note/DM00042534.pdf
Application note | http://www.st.com/resource/en/application_note/DM00072315.pdf
Application note | http://www.st.com/resource/en/application_note/DM00073742.pdf
Application note | http://www.st.com/resource/en/application_note/DM00073853.pdf
Application note | http://www.st.com/resource/en/application_note/DM00080497.pdf
Application note | http://www.st.com/resource/en/application_note/DM00081379.pdf
Application note | http://www.st.com/resource/en/application_note/DM00085385.pdf
Application note | http://www.st.com/resource/en/application_note/DM00087593.pdf
Application note | http://www.st.com/resource/en/application_note/DM00125306.pdf
Application note | http://www.st.com/resource/en/application_note/DM00129215.pdf
Application note | http://www.st.com/resource/en/application_note/DM00141025.pdf
Application note | http://www.st.com/resource/en/application_note/DM00144612.pdf
Application note | http://www.st.com/resource/en/application_note/DM00148033.pdf
Application note | http://www.st.com/resource/en/application_note/DM00150423.pdf

Application note | http://www.st.com/resource/en/application_note/DM00151811.pdf
Application note | http://www.st.com/resource/en/application_note/DM00156964.pdf
Application note | http://www.st.com/resource/en/application_note/DM00160482.pdf
Application note | http://www.st.com/resource/en/application_note/DM00209748.pdf
Application note | http://www.st.com/resource/en/application_note/DM00209768.pdf
Application note | http://www.st.com/resource/en/application_note/DM00209772.pdf
Application note | http://www.st.com/resource/en/application_note/DM00216518.pdf
Application note | http://www.st.com/resource/en/application_note/DM00220769.pdf
Application note | http://www.st.com/resource/en/application_note/DM00226326.pdf
Application note | http://www.st.com/resource/en/application_note/DM00227538.pdf
Application note | http://www.st.com/resource/en/application_note/DM00236305.pdf
Application note | http://www.st.com/resource/en/application_note/DM00257177.pdf
Application note | http://www.st.com/resource/en/application_note/DM00260952.pdf
Application note | http://www.st.com/resource/en/application_note/DM00263732.pdf
Application note | http://www.st.com/resource/en/application_note/DM00269143.pdf
Application note | http://www.st.com/resource/en/application_note/DM00269146.pdf
Application note | http://www.st.com/resource/en/application_note/DM00272912.pdf
Application note | http://www.st.com/resource/en/application_note/DM00311483.pdf
Application note | http://www.st.com/resource/en/application_note/DM00315319.pdf
Application note | http://www.st.com/resource/en/application_note/DM00327191.pdf
Application note | http://www.st.com/resource/en/application_note/DM00354244.pdf
Application note | http://www.st.com/resource/en/application_note/DM00354333.pdf
Application note | http://www.st.com/resource/en/application_note/DM00355687.pdf
Application note | http://www.st.com/resource/en/application_note/DM00367673.pdf
Application note | http://www.st.com/resource/en/application_note/DM00380469.pdf
Application note | http://www.st.com/resource/en/application_note/DM00395696.pdf
Application note | http://www.st.com/resource/en/application_note/DM00445657.pdf
Application note | http://www.st.com/resource/en/application_note/DM00476869.pdf
Application note | http://www.st.com/resource/en/application_note/DM00493651.pdf
Application note | http://www.st.com/resource/en/application_note/DM00536349.pdf
Application note | http://www.st.com/resource/en/application_note/DM00660597.pdf

## Application note http://www.st.com/resource/en/application_note/DM00725181.pdf

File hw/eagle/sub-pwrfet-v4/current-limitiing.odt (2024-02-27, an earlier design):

Ref: eagle schematic image: bmsmot/hw/eagle/sub-pwrfet-v4 (240108)

Overall:

The goal of this version is to include current limiting to pwm’ing a half-bridge powering a dc motor, in order to avoid large currents during the motor startup. To do this a comparator and logic gates are added to a sub-board that receives a pwm signal (0-5v), such as from the bmsmot board.

A half-bridge has a current sense resistor in the low-side fet source, and a comparator triggers when the current exceeds the limit. When that happens a latch is set that holds the fet driver input high (which sets the low side fet OFF) until the pwm cycle ends. When the pwm ON duration ends the latch is reset. (Which means that the maximum pwm duty cycle has to be less than 100%. A continuous pwm signal ON will never reset the latch once it is set, but 99% ON with 20KHz pwm frame rate has an off duration that is more than sufficient to reset the latch, given the opto-isolator rise/falls specs.)

There are two ways to connect the motor. One is for the motor to connect to the half-bridge FET hi/lo junction and power plus, the other is to connect to hi/lo and power minus. Which connection is used determines whether the fet driver IN signal is inverted, and which half-bridge FET is ON when the pwm is OFF.

Connecting the motor plus/minus to power plus/half-bridge-junction allows daisy-chaining the plus power to the multiple motors. The minus of the motors all go to their respective sub-boards, and the minus connection on the sub-boards goes through a current sense resistor to the low side FET. Connecting the motor plus/minus to half-bridge-junction/minus will not permit daisy-chaining the minus as the current sense is in the minus side and putting current sense in the plus side is not practical. Hence, the better approach is for the motors to connect to plus power and the minus to the sub-boards.

Opto-isolator and pwm signal--

From the bmsmot board the start of the ON (high) duration of a pwm frame drives the gate to FET3 which turns the LED in the H11L1S opto-isolator ON, and the H11L1S output goes low. When the pwm signal is OFF, the H11L1S output is high.

Current limiting Comparator--

The AP331 comparator requires a pull-up. When the plus input voltage is higher than the minus input the output is high. The plus input is the voltage of the current sense resistor. (R3, a 5 mOhm resistor with 10a is 10 mv and 0.5W.) The minus input is the regulated 5v divider.

The comparator trigger point is set by R14 and R13. When the current sense resistor voltage exceeds the trigger point, the output goes high, and R11 raises plus input voltage slightly which provides hysteresis (recommended on the datasheet) which avoids oscillations around the trigger point.

Initial conditions--

Start with the pwm signal off, i.e. low, and the current sense voltage zero (i.e. no current). The opto output is high. The comparator output is low.

The latch formed with nor gates 2 & 3 is in what we will call the reset state. The opto output is high which makes 1 and 2 outputs low.

Nor 1 has the opto input high, so 1's output is low. Nor 4 inverts and its output drives the FET driver IN high. The FET driver with IN high turns on the high-side FET and turns off the low-side FET, if the bootstrap cap is charged. If the capacitor is not charged, since initially the pwm has not started neither bridge FET is turned on. All is quiet.

Nor 3 input has nor 2's output low and the other nor 3 input has the comparator output low, so 3's output is high. This will hold nor 2's output low when the pwm signal turns ON and the opto's output goes low.

PWM ON--

Now the pwm signal goes high and the opto output goes low. Nor 1 has both inputs low so nor 1's output goes high; inverts with 4. The 4's output low to the fet driver IN turns the low side FET ON and the high side OFF. (That causes the hi/lo side FET junction to be low which charges the bootstrap capacitor.)

The current begins increasing. If the current sense resistor voltage trips the comparator, the comparator output goes high. Nor3's output goes low. Nor 2 now has both inputs low, so it goes high and its high causes nor 1 go to low. That inverts and the fet driver IN goes high. This turns off the low side FET and turns on the high side FET.

The current begins to decrease. At some point the comparator turns OFF, so it's output goes low. Nor 3's output will be held low by nor 2's output being high; the opto's output is still low since the pwm is still ON. That state remains until the pwm ON duration ends and the opto output goes high.

If the comparator was tripped and the current has not decreased below the hysteresis level before the pwm cycle ends, the next pwm ON duration starts with one input to both nor 2 and nor 3 high, i.e. the opto output is high and was high before the next pwm frame starts, and the comparator is still on, so 3's output is low. When that happens, nor 1, 2, and 3 have their outputs low. When the pwm transitions to ON the opto output goes high to low. Nor 2's output was low before the transition (since it was held low by the opto output being high with the pwm off). Nor 1 will have a brief high output until nor 2 output goes high. When the comparator turns off there is no change and nor 1 remains low until the next pwm starts. In summary, if the current is above the trip point when a pwm frame starts the driver is off for the entire frame.

Power supplies--

Even though the power supply is expected to nominally 12v, with a steady state max of about 13.8v, inductive transients may raise that somewhat. Sudden drops in the pwm to the motor could cause the motor inertia to pump current back into the power supply and possibly raise the 12v power bus substantially; theoretically it could double the voltage. The first sub-board based on the AURIS2110 driver connected directly to the 12v. When the motor was connected and manually switched on/off the TLP151 iso-coupler lit up and smoked gloriously. Suspecting some sort of transient a 12v LM type regulator was horribly hacked into the board. It shouldn’t be needed for the TLP151 as it should withstand 35v on the Vcc, but it could be that AURIS driver went south and blew the TLP151 via the ouput pin. The half bridge drivers usually have Vcc max voltages around 15-20v. So to be safe the LM7812 regulator is included, but may not be necessary.

A bead/resistor and caps are there jic there are some spikes on the power input. There are footprints on the pcb for LM7812 (TO-220) and LM78L12 (TO-93) since there are plenty of LM7812s in "the box”. The ‘L version is smaller and not so ugly.

An option to power the logic and driver from a 1W isolated dc-dc convertor was added should a high voltage be used with the half-bridge. However, it is likely that such an application would require revisions of the high & low side FET footprints. With the dc-dc convertor the 12v regulator parts would not be needed.

page 3 Pwrfet-v4 sub-board logic description 01/10/24

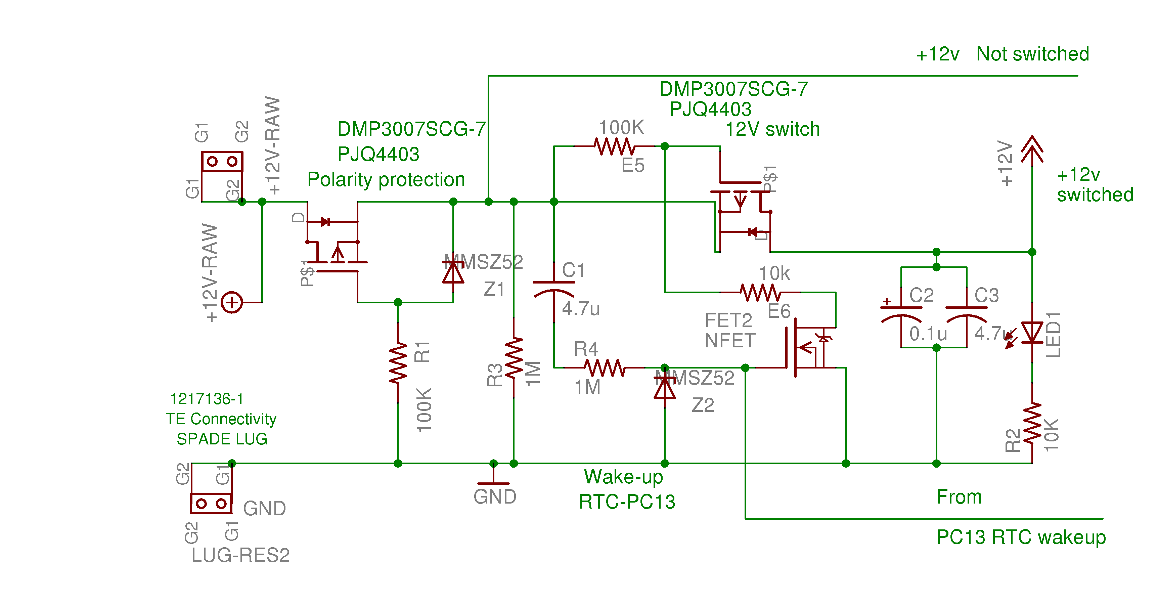
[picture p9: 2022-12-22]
hw/eagle/clip/polarityswitch.png

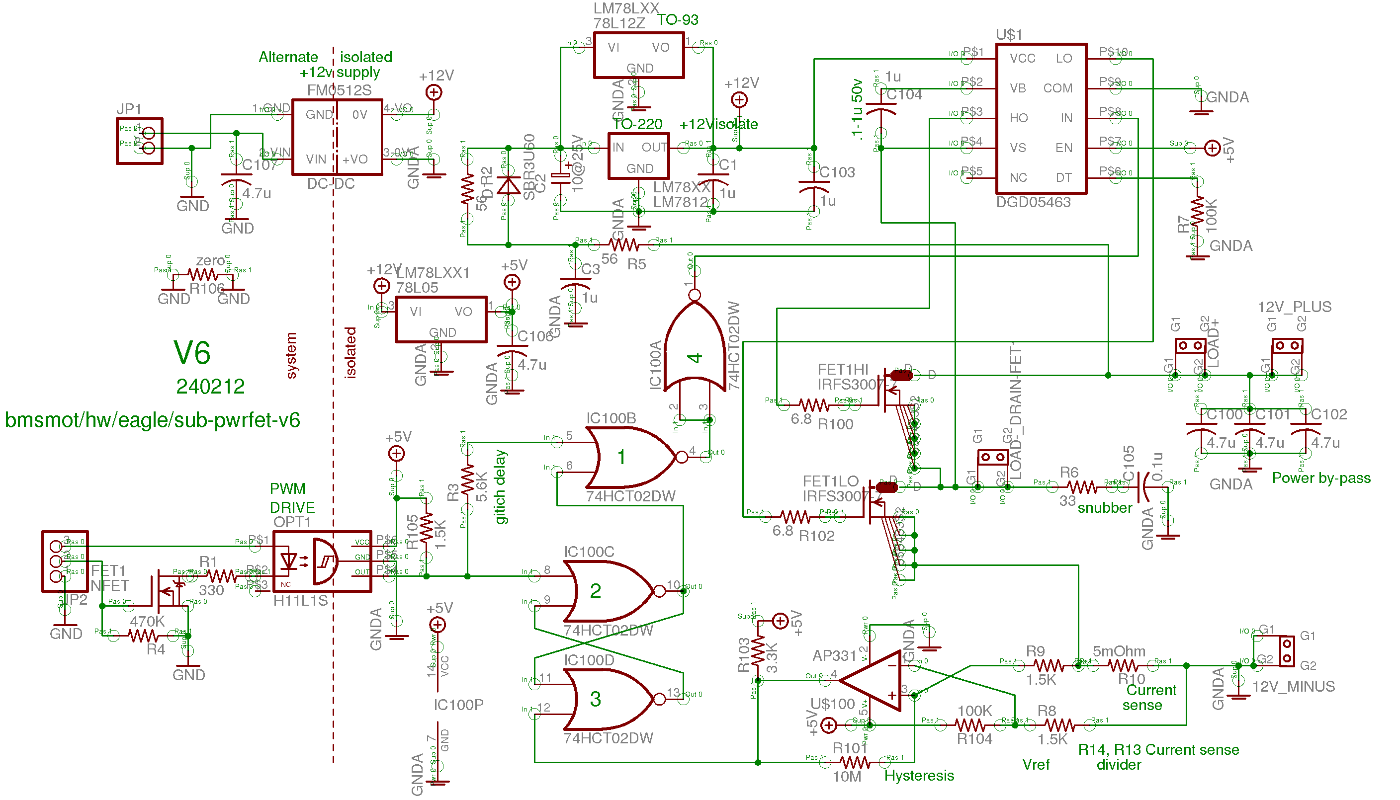
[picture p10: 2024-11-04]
hw/eagle/sub-pwrfet-v6/v6-sch.png

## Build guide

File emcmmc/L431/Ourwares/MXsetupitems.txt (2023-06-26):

MXsetupitems.txt

Items

1. Serial 

The last argument must match what was setup in 'MX--

/* Add bcb circular buffer to SerialTaskSend for usart1 */
	#define NUMCIRBCB1  16 // Size of circular buffer of BCB for usart6
	ret = xSerialTaskSendAdd(&huart1, NUMCIRBCB1, 1); // dma
	if (ret < 0) morse_trap(1); // Panic LED flashing

2. ADC

In adcparams.h the size must match 'MX--

#define ADC1IDX_ADCSCANSIZE   6 // Number ADC channels read

3.  morse.c

The LED set/reset must match the board, i.e. is the LED energized
by pull-down or pull-up.

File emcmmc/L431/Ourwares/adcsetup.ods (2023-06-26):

 | mxusartusbcan |  | From datasheet formula
 | adc setup |  | Section | 5.3.21
 | 02/02/19 |  | 12-bit ADC | characteristics
 |  | Bus | 84
 |  | Divider | 8
 | K(sampling) | C(pf) | fadc*MHz) | 12bit | Rain |  | Sample tiime
 | 3 | 5 | 10.5 | 9.7040605278 | 5.79 |  | 0.3
 | 15 | 5 | 10.5 | 9.7040605278 | 29.34 |  | 1.4
 | 28 | 5 | 10.5 | 9.7040605278 | 54.86 |  | 2.7
 | 56 | 5 | 10.5 | 9.7040605278 | 109.82 |  | 5.3 |  |  | cts/volt
 | 84 | 5 | 10.5 | 9.7040605278 | 164.78 |  | 8.0 |  |  | 819 | 2.5 | 2047.5 | 2047.5
 | 112 | 5 | 10.5 | 9.7040605278 | 219.74 |  | 10.7 |  |  |  | 2047 | 1842.3
 | 144 | 5 | 10.5 | 9.7040605278 | 282.55 |  | 13.7
dynamometer | 480 | 5 | 10.5 | 9.7040605278 | 942.07 |  | 45.7
'MX
03/15/19 |  |  | ADC | Sample cycles | conv (us) |  |  | Offset | divider | Sensor amps | scale
 | PA1 | IN1 | 1 | 56 | 6.4761904762 |  | spare | ADC cts |  |  | amps
 | PA5 | IN5 | 2 | 56 | 6.4761904762 |  | Total battery current | 2047 | 0.6444444444 | 200 | 0.1086 |  | ACS770ECB-200B-PFF-T
 | PA6 | IN6 | 3 | 56 | 6.4761904762 |  | Current #1 motor | 2047 | 0.6444444444 | 600 | 0.3257 |  | L01Z600S05
 | PA7 | IN7 | 4 | 56 | 6.4761904762 |  | Current #2 motor | 2047 | 0.6444444444 | 400 | 0.2172 |  | L01Z400S05
 | PB0 | IN8 | 5 | 56 | 6.4761904762 |  | Speed control pot
 | PC1 | IN11 | 6 | 56 | 6.4761904762 |  | Control level (Hall sensor)
 | PC2 | IN12 | 7 | 56 | 6.4761904762 |  | +12 volt supply raw | 0 | 0.1525423729 | 19.0111111111
 | PC5 | IN15 | 8 | 56 | 6.4761904762 |  | +5 sensor supply voltage | 0 | 0.5465116279 | 5.3063829787
 |  | Temp | 9 | 480 | 46.8571428571 |  | Internal temperature sensor
 |  | Vref | 10 | 480 | 46.8571428571 |  | Internal voltage reference
 |  |  | DMA buffer | Num seq | 16
 |  |  |  | Total size | 320 |  |  | 10 | 10 | 0.5000 | 2.5000
 |  |  |  |  |  |  |  | 8.2 | 10 | 0.5495 | 2.7473
 |  |  |  | Time per seq | 145.5238095238 |  |  | 6.8 | 10 | 0.5952 | 2.9762
 |  |  | DMA buffer | Num seq | 16 | Per ½ dma
 |  |  |  | Per dma | 2328.380952381 | 1164.1904761905
 |  |  |  |  | 858.9659685864
 |  |  |  |  | DMA interrupt
 |  |  |  |  | Per sec | us per
 |  |  |  |  | 859 | 1164.1443538999

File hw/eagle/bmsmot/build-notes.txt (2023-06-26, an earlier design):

build-notes.txt

06/18/2023

1. Voltage divider
R15 - 110K
R14 - 28.7K

2. 0.1 instead of 50n
C103,C104,C105

2. H11L1 - Need pullups

- The output is open drain and needs a
pullup. The processor internal pullup
is weak.

- 5.6K tacked to pins was used.

3. AC-DET H11L1 gnd & output error

- Hack needed to reverse GND and output.

4. 'V1 pcb layout was updated for pullups
and AC-DET wiring.

5. Hack for keyswitch 

R104 and D100 serve to turn on PFET 12v
power switch.

- Remove R104 & D100.
- Add NFET with +/- Vgs across D100 pads
(gnd and gate). 
- Cut trace going to PA12 
- Jumper wire from PA12 side of cut to
NFET drain.
- Update eagle bmsmot-v1

6. Coin-cell polarity protection

Added 18K resistor in + trace to prevent
reversed coin-cell insertion from damaging
processor via VBAT.

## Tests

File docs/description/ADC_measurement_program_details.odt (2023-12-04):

Overall--

Goal: ADC measurement of AC input where the AC input to the ADC is offset, and there is a separate zero-crossing interrupt that marks the point where the AC passes through zero, (or at least at some level each cycle).

DMA stores ADC2 readings continuously in a circular buffer. The DMA interrupts at the half, and full buffer points, which triggers a notification to ADCTask.

EXTI10-15 interrupt stores the current DTW system timer and computes the difference between the new and previous interrupts. That produces a count of the number of system ticks during one AC cycle.

The ADC2 sample duration selection (i.e. eight possibilities: 3,15,26,56,84,112,144,480) plus the 12 ADC cycle fixed duration times the division ratio between the system clock and the ADC clock, e.g. 16, determines the number of system ticks per ADC conversion.

The number of system ticks for one cycle determines when, in the ADCTask processing of the DMA buffer, the end/beginning of an AC cycle was marked by the EXTI interrupt.

The computation of an AC cycle is based on--

1) the number of ADC readings during the cycle

2) the sum of the readings

3) the sum of the (readings – offset) squared.

Dividing 3) by 1) and taking the square root produces the rms value.

Dividing 2) by 1) produces the offset.

The offset is initially set from the parameter file. By filtering the computed offset over a period of time the offset can be adjusted for drift.

ASM—fast512summing.S

This is an assembly routine for fast inline summing of a DMA buffer, and called from ADCTask.

ADCTask calls fast512summing with a pointer to the following struct, and an index into the DMA buffer. (buffer size – index) determines the number of readings summed.

Upon entry r0 holds the pointer to the struct, and r1 holds the index. The routine updates adc2ctr in the struct with the number that will be summed; computes a jump address and jumps to the inline code at the location to sum the number of readings called for.

Before exiting this routine updates the struct with the new sums, and the pointer into the DMA buffer.

struct SUMSQBUNDLE

{

uint64_t sumsq; // Sum of (reading - offset)^2

uint16_t* pdma; // Ptr to dma buffer

uint16_t* pdma_end; // Ptr to dma buffer end+1

uint32_t adcaccum; // Sum of readings

uint32_t adc2ctr; // Running count of readings in both sums

uint32_t offset; // ADC2 offset with zero input

uint16_t n; // Number of readings to sum

};

ADCTask ADC2 notifications--

ADCTask handles both ADC1 and ADC2. The two ADCs run independently. The half DMA buffer interrupt and full DMA buffer interrupt trigger two notification bits for ADC1, and two for ADC2. With these, the ADCTask code can set a pointer to the DMA half-buffer that was just filled.

ADC1 measures 12 inputs and the DMA buffer is set to repeat 16 times before interrupting. Inline C code sums the DMA buffer for each of the 12 inputs.

For ADC2 the DMA buffer is summed with the fast assembly code. If the end of a zero crossing is encountered the DMA buffer is summed up to that point and the 'cycle_end' routine is called that computes differences in the sums and sets the next end point. Following this the remainder of the DMA buffer is summed. If there is no end-point contained in the DMA buffer the entire buffer is summed.

ADC2 buffering--

Since the ASM routine uses inline coding it needs to know the size of the buffer. ‘fast512summing.h’ file supplies a #define that specifies the half-dma buffer size in terms of half-words. (The DMA uses “items” in its counter and items can be words, half-words, or bytes. E.g. the ADC is two bytes, so 512 would specify a half buffer size of 1024 bytes, or a full buffer of 2048 bytes.

Changing the buffer size involves changing the one #defines in ‘fast512summing.h’. The C code uses this #define for sizing.

ADC2 sampling--

The rate that the ADC makes a conversion is determined by the ADC clock frequency and the sample duration selected. The ADC clock has to be below 30 MHz. With the system running at max rate, 180MHz, the PCLK2 frequency is 45 MHz. The ADC prescalar can be 2, 4, 6,or 8. With 4 selected the ADC clock runs at 11.25MHz. It could be 22.5 MHz, but there is also an issue of the sample selection needing to be long enough to fully charge the sampling capacitance, given the input impedance.

The initialization of ADCTask computes the number of system clock ticks per ADC conversion, given the initialization done when ‘main’ starts. The sampling duration in STM32CubeMX will result in the initialization setting up the system clock ticks per ADC conversion.

Page 2 12/02/23 ADC details

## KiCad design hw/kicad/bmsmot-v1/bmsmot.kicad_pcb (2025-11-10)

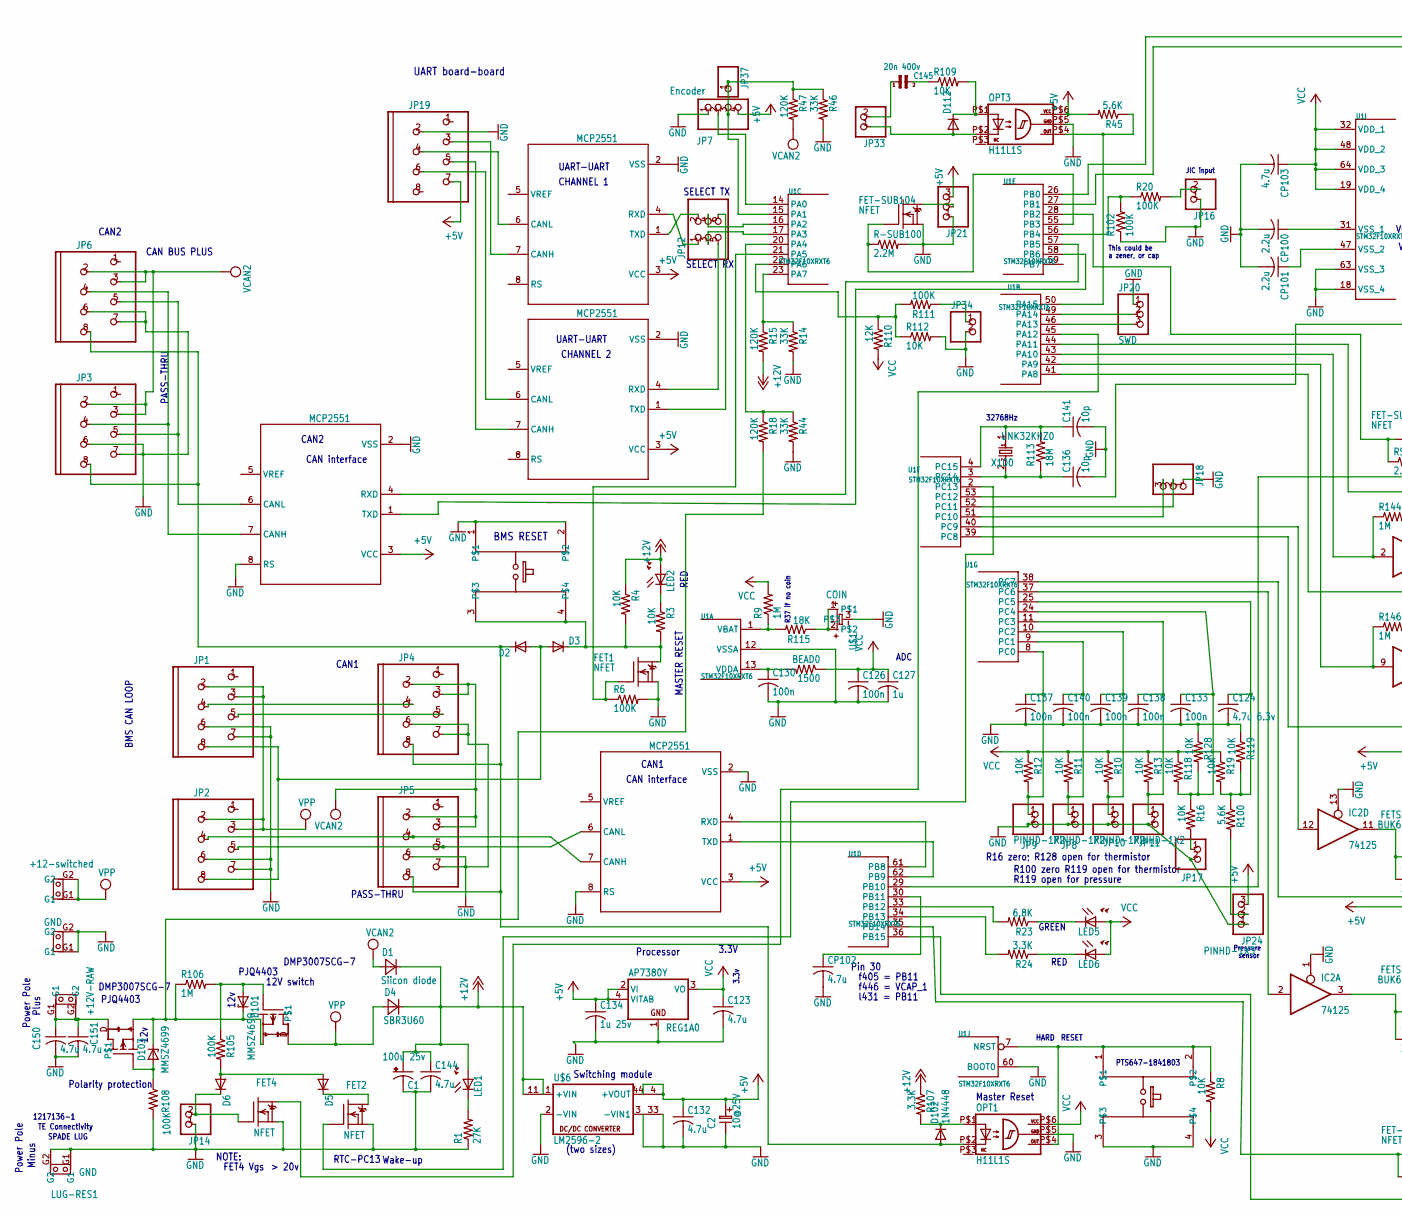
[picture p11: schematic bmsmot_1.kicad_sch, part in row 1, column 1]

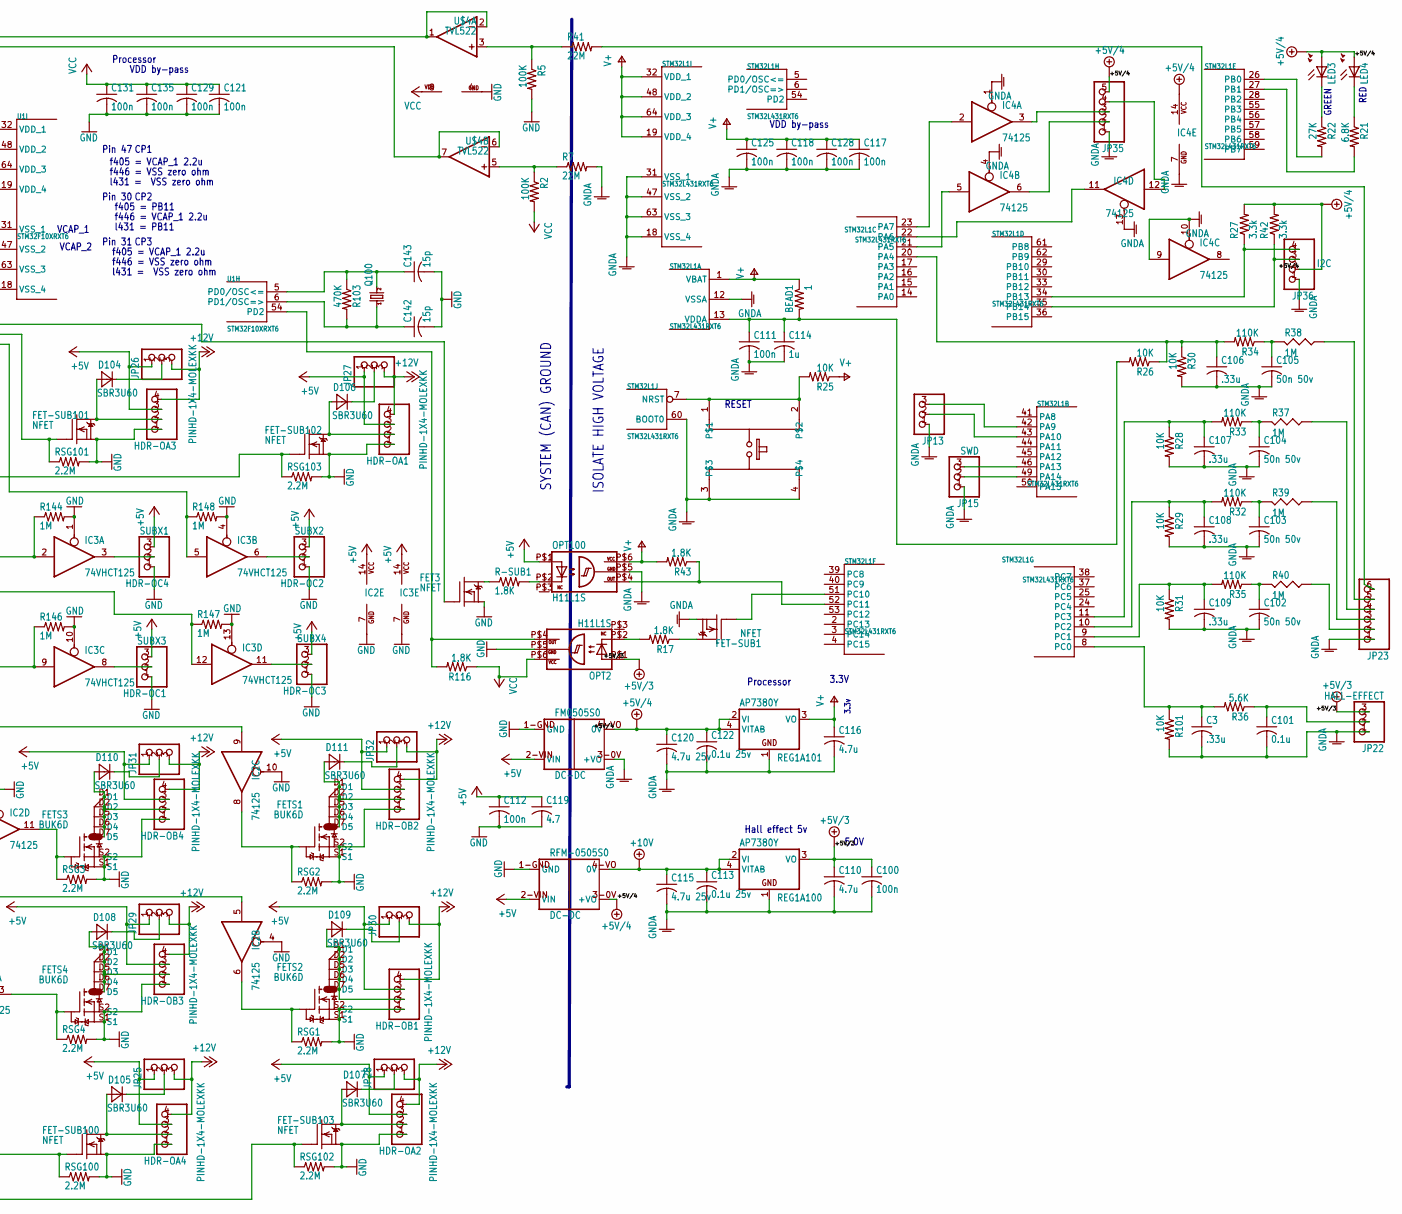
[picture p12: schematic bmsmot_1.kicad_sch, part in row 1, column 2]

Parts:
+12SW0: +12-switched; SPADE_TAB
BEAD0: 1500; R0603
BEAD1: 1; R0603
BMS-RESET0: E-SWITCH2
C1: 100u 25v; E5-8,5
C2: 10@25V; ES-2,5L
C3, C106, C107, C108, C109: .33u; C0603
C100, C111, C112, C117, C118, C121, C125, C126, C128, C129, C130, C131, C133, C135, C137, C138, C139, C140: 100n; C0603
C101: 0.1u; C0603
C102, C103, C104, C105: 50n 50v; C0603
C110, C116, C123, C132: 4.7u; C0603
C113, C122: 0.1u 25v; C0603
C114, C127: 1u; C0603
C115, C120: 4.7u 25v; C0805
C119: 4.7; C0805
C124: 4.7u 6.3v; C0603
C134: 1u 25v; C0603
C136, C141: 10p; C0603
C142, C143: 15p; C0603
C144, C150, C151: 4.7u; C0805
C145: 20n 400v; 1210
CP100, CP101: 2.2u; C0603
CP102, CP103: 4.7u; C0603
D1: Siicon diode; POWERDI123
D2, D3, D5, D6, D112: DIODE-SOD323-R; SOD323-R
D4, D104, D105, D106, D107, D108, D109, D110, D111: SBR3U60; POWERDI123
D101, D103: MMSZ4699; SOD80C
D102: 1N4448; SOD123
FET1, FET2, FET3, FET4: NFET; SOT-23
FET-SUB1, FET-SUB100, FET-SUB101, FET-SUB102, FET-SUB103, FET-SUB104: NFET; SOT-23
FETS1, FETS2, FETS3, FETS4: BUK6D; DFN2020-6
FM0505S0: DC-DC
GND0: GND; SPADE_TAB
HDR-OA1, HDR-OA2, HDR-OA3, HDR-OA4: PINHD-1X4-MOLEXKK; 1X4-MOLEXKK
HDR-OB1, HDR-OB2, HDR-OB3, HDR-OB4: PINHD-1X4-MOLEXKK; 1X4-MOLEXKK
HDR-OC1: SUBX3; 1X03
HDR-OC2: SUBX2; 1X03
HDR-OC3: SUBX4; 1X03
HDR-OC4: SUBX1; 1X03
IC1, IC100, IC101, IC102: MCP2551; SO-08
IC2, IC4: 74125; TSSOP14
IC3: 74VHCT125; TSSOP14
JP1, JP2, JP3, JP4, JP5, JP6, JP19: MOD8P8C
JP7: Encoder; 1X04
JP8, JP9, JP10, JP11, JP14, JP16, JP17, JP33, JP34: PINHD-1X2; 1X02
JP12: PINHD-2X3; 2X03
JP13, JP18, JP21, JP24, JP25, JP26, JP27, JP28, JP29, JP30, JP31, JP32: PINHD-1X3; 1X03
JP15, JP20: SWD; 1X03
JP22: HALL-EFFECT; 1X03
JP23: PINHD-1X6; 1X06
JP35: PINHD-1X5; 1X05
JP36: I2C; 1X04
JP37: PINHD-1X1; 1X01
LED1, LED2, LED3, LED4, LED5, LED6: LEDCHIP-LED0603; CHIP-LED0603
LUG-GND1: +12V-RAW; SPADE_TAB
LUG-RES1: GND; SPADE_TAB
OPT1, OPT2, OPT3, OPT100: H11L1S; SMD-6
Q100: CRYTALHC49S; HC49_S
R1, R22: 27K; R0603
R2, R5, R6, R20, R102, R105, R108, R111: 100K; R0603
R3, R4, R8, R10, R11, R12, R13, R16, R19, R25, R26, R28, R29, R30, R31, R101, R109, R112, R118, R119, R128: 10K; R0603
R7, R41: 22M; 0207_5V
R9, R106: 1M; R0603
R14, R44, R46: 33K; R0603
R15, R18, R47: 120K; R0603
R17, R43, R116: 1.8K; R0603
R21, R23: 6.8K; R0603
R24, R107: 3.3K; R0603
R27, R42: 3.3k; R0603
R32, R33, R34, R35: 110K; R0603
R36, R45, R100: 5.6K; R0603
R37, R38, R39, R40: 1M; RS-2,5
R103: 470K; R0603
R110: 12K; R0603
R113: 18M; R0603
R115: 18K; R0603
R144, R146, R147, R148: 1M; R0402
R-SUB1: 1.8K; R0603
R-SUB100: 2.2M; R0603
REG1A0, REG1A100, REG1A101: AP7380Y; SOT89
RESET0, RESET1: E-SWITCH2
RFM-0505S0: DC-DC
RSG1, RSG2, RSG3, RSG4, RSG100, RSG101, RSG102, RSG103: 2.2M; R0603
STM32L1: STM32L431RXT6; TQFP64
U1: STM32F10XRXT6; TQFP64
U$1: COIN
U$2, U$3: PJQ4403P; DFN3333-8L
U$4: TVL522; VSSOP8
U$6: LM2596-2; LM2569SW2
UNK32KHZ0: X100; 32KHZ

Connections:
+5V: C2.1, C112.1, C119.1, C132.1, C134.1, FM0505S0.2-VIN (VIN), HDR-OA1.3, HDR-OA2.3, HDR-OA3.3, HDR-OA4.3, HDR-OB1.3, HDR-OB2.3, HDR-OB3.3, HDR-OB4.3, HDR-OC1.3, HDR-OC2.3, HDR-OC3.3, HDR-OC4.3, IC1.3 (VCC), IC2.14 (VCC), IC3.14 (VCC), IC100.3 (VCC), IC101.3 (VCC), IC102.3 (VCC), JP7.4, JP19.7 (4), JP21.3, JP24.3, JP25.1, JP26.1, JP27.1, JP28.1, JP29.1, JP30.1, JP31.1, JP32.1, OPT3.P$6 (VCC), OPT100.P$1 (A), R45.2, REG1A0.2 (VI), REG1A0.4 (VITAB), RFM-0505S0.2-VIN (VIN), U$6.4 (+VOUT1), U$6.44 (+VOUT)
+5V/3: C100.1, C110.1, JP22.3, OPT2.P$1 (A), REG1A100.3 (VO)
+5V/4: C120.1, C122.1, FM0505S0.4-VO (0V), IC4.14 (VCC), JP35.5, JP36.2, LED3.A, LED4.A, R27.2, R42.2, REG1A101.2 (VI), REG1A101.4 (VITAB), RFM-0505S0.3-0V (+VO)
+10V: C113.1, C115.1, REG1A100.2 (VI), REG1A100.4 (VITAB), RFM-0505S0.4-VO (0V)
+12V: C1.+, C144.1, D1.C, D4.C, HDR-OA1.4, HDR-OA2.4, HDR-OA3.4, HDR-OA4.4, HDR-OB1.4, HDR-OB2.4, HDR-OB3.4, HDR-OB4.4, JP25.3, JP26.3, JP27.3, JP28.3, JP29.3, JP30.3, JP31.3, JP32.3, LED1.A, LED2.A, R4.1, R15.2, R107.1, U$6.1 (+VIN), U$6.11 (+VIN1)
+12V-POLARITY: D101.C, D103.C, R18.2, R106.1, U$2.S (S3), U$3.S (S3)
+12V-RAW: C150.1, C151.1, LUG-GND1.G1, LUG-GND1.G2, U$2.D
AC-12VRMS: JP34.1, R111.1
AC-OPTO-1: D112.A, JP33.1, OPT3.P$2 (C)
AC-OPTO-2: C145.1, JP33.2
AC-OPTO-IN: D112.C, OPT3.P$1 (A), R109.2
AC-OPTO-RC: C145.2, R109.1
BUFF1-PC8: IC2.9 (I), U1.39 (PC8)
BUFF2-PC7: IC2.5 (I), U1.38 (PC7)
BUFF5-PC9: IC2.12 (I), U1.40 (PC9)
BUFF6-PC6: IC2.2 (I), U1.37 (PC6)
CANH1: IC102.7 (CANH), JP2.4 (6), JP5.4 (6)
CANH1-FT: JP1.4 (6), JP4.4 (6)
CANH2: IC1.7 (CANH), JP3.4 (6), JP6.4 (6)
CANL1: IC102.6 (CANL), JP2.5 (3), JP5.5 (3)
CANL1-FT: JP1.5 (3), JP4.5 (3)
CANL2: IC1.6 (CANL), JP3.5 (3), JP6.5 (3)
CHAN1-RX: IC100.4 (RXD), JP12.1
CHAN1-TX: IC100.1 (TXD), JP12.2
CHAN1_CAN-L: IC100.6 (CANL), JP19.4 (6)
CHAN2-RX: IC101.4 (RXD), JP12.5
CHAN2-TX: IC101.1 (TXD), JP12.6
CHAN2_CAN-H: IC101.7 (CANH), JP19.5 (3)
CHAN2_CAN-L: IC101.6 (CANL), JP19.6 (7)
CHAN-1_CAN-H: IC100.7 (CANH), JP19.3 (2)
COIN+: R115.1, U$1.1, U$1.2
DRAIN-SUB1: D111.A, FETS1.D1, FETS1.D2, FETS1.D5 (D3), FETS1.D6 (D4), FETS1.D7 (D5), HDR-OB2.2
DRAIN-SUB2: D109.A, FETS2.D1, FETS2.D2, FETS2.D5 (D3), FETS2.D6 (D4), FETS2.D7 (D5), HDR-OB1.2
DRAIN-SUB5: D110.A, FETS3.D1, FETS3.D2, FETS3.D5 (D3), FETS3.D6 (D4), FETS3.D7 (D5), HDR-OB4.2
DRAIN-SUB6: D108.A, FETS4.D1, FETS4.D2, FETS4.D5 (D3), FETS4.D6 (D4), FETS4.D7 (D5), HDR-OB3.2
DRAIN-SUB13: D107.A, FET-SUB103.3 (D), HDR-OA2.2
DRAIN-SUB14: D106.A, FET-SUB102.3 (D), HDR-OA1.2
DRAIN-SUB17: D104.A, FET-SUB101.3 (D), HDR-OA3.2
DRAIN-SUB18: D105.A, FET-SUB100.3 (D), HDR-OA4.2
DSEL-OA1: D106.C, JP27.2
DSEL-OA2: D107.C, JP28.2
DSEL-OA3: D104.C, JP26.2
DSEL-OA4: D105.C, JP25.2
DSEL-OB1: D109.C, JP30.2
DSEL-OB2: D111.C, JP32.2
DSEL-OB3: D108.C, JP29.2
DSEL-OB4: D110.C, JP31.2
FET1-DRAIN-MASTER-RESET: BMS-RESET0.3, BMS-RESET0.4, D3.C, FET1.3 (D), R3.2, R4.2
FET2-DRAIN: D5.C, FET2.3 (D)
FET3-DRAIN-UART5-TX: FET3.3 (D), R-SUB1.1
FET103-GATE: D103.A, R108.1, U$2.G
FET-SUB9-DRAIN: FET-SUB104.3 (D), JP21.2
GATE-SUB4-PB10: FET-SUB102.1 (G), RSG103.1, U1.29 (PB10)
GATE-SUB7-PB2: FET-SUB101.1 (G), RSG101.1, U1.28 (PB2)
GATE-SUBH3-PB15: FET-SUB103.1 (G), RSG102.1, U1.36 (PB15)
GATE-SUBH8-PB14: FET-SUB100.1 (G), RSG100.1, U1.35 (PB14)
GND: BMS-RESET0.1, BMS-RESET0.2, C1.-, C2.2, C112.2, C119.2, C121.2, C123.2, C124.2, C126.2, C127.2, C129.2, C130.2, C131.2, C132.2, C133.2, C134.2, C135.2, C136.2, C137.2, C138.2, C139.2, C140.2, C141.2, C142.2, C143.2, C144.2, C150.2, C151.2, CP100.2, CP101.2, CP102.2, CP103.2, FET1.2 (S), FET2.2 (S), FET3.2 (S), FET4.2 (S), FET-SUB100.2 (S), FET-SUB101.2 (S), FET-SUB102.2 (S), FET-SUB103.2 (S), FET-SUB104.2 (S), FETS1.S1, FETS1.S2, FETS2.S1, FETS2.S2, FETS3.S1, FETS3.S2, FETS4.S1, FETS4.S2, FM0505S0.1-GND (GND), GND0.G1, GND0.G2, HDR-OA1.1, HDR-OA2.1, HDR-OA3.1, HDR-OA4.1, HDR-OB1.1, HDR-OB2.1, HDR-OB3.1, HDR-OB4.1, HDR-OC1.1, HDR-OC2.1, HDR-OC3.1, HDR-OC4.1, IC1.2 (VSS), IC1.8 (RS), IC2.1 (OE), IC2.4 (OE), IC2.7 (GND), IC2.10 (OE), IC2.13 (OE), IC3.1 (OE), IC3.4 (OE), IC3.7 (GND), IC3.10 (OE), IC3.13 (OE), IC100.2 (VSS), IC101.2 (VSS), IC102.2 (VSS), IC102.8 (RS), JP1.6 (7), JP1.7 (4), JP2.6 (7), JP2.7 (4), JP3.6 (7), JP3.7 (4), JP4.6 (7), JP4.7 (4), JP5.6 (7), JP5.7 (4), JP6.6 (7), JP6.7 (4), JP7.1, JP8.2, JP9.2, JP10.2, JP11.2, JP14.1, JP16.1, JP17.2, JP18.1, JP19.2 (5), JP20.1, JP21.1, JP24.1, JP34.2, LUG-RES1.G1, LUG-RES1.G2, OPT1.P$5 (GND), OPT2.P$5 (GND), OPT3.P$5 (GND), R1.1, R5.2, R6.2, R14.2, R44.2, R46.2, R102.1, R108.2, R112.2, R119.1, R128.1, R144.2, R146.2, R147.2, R148.2, R-SUB100.2, REG1A0.1 (GND), RESET0.3, RESET0.4, RFM-0505S0.1-GND (GND), RSG1.2, RSG2.2, RSG3.2, RSG4.2, RSG100.2, RSG101.2, RSG102.2, RSG103.2, U1.12 (VSSA), U1.18 (VSS_4), U1.60 (BOOT0), U1.63 (VSS_3), U$1.3, U$4.4 (GND), U$6.2 (-VIN), U$6.3 (-VIN1), U$6.33 (-VIN2)
GNDA: C3.2, C100.2, C101.2, C102.2, C103.2, C104.2, C105.2, C106.2, C107.2, C108.2, C109.2, C110.2, C111.2, C113.2, C114.2, C115.2, C116.2, C117.2, C118.2, C120.2, C122.2, C125.2, C128.2, FET-SUB1.2 (S), FM0505S0.3-0V (+VO), IC4.1 (OE), IC4.4 (OE), IC4.7 (GND), IC4.9 (I), IC4.10 (OE), IC4.13 (OE), JP13.1, JP15.1, JP22.1, JP23.1, JP35.1, JP36.1, OPT100.P$5 (GND), R7.2, R28.2, R29.2, R30.2, R31.2, R101.2, REG1A100.1 (GND), REG1A101.1 (GND), RESET1.3, RESET1.4, STM32L1.12 (VSSA), STM32L1.18 (VSS_4), STM32L1.31 (VSS_1), STM32L1.47 (VSS_2), STM32L1.60 (BOOT0), STM32L1.63 (VSS_3)
HDRXA1: HDR-OC1.2, IC3.8 (O)
HDRXA2: HDR-OC2.2, IC3.6 (O)
HDRXA3: HDR-OC3.2, IC3.11 (O)
HDRXA4: HDR-OC4.2, IC3.3 (O)
HV1: JP23.4, R37.1
HV1-1: C104.1, R33.1, R37.2
HV1-2: C103.1, R32.1, R39.2
HV1-3: C102.1, R35.1, R40.2
HV1-4: C105.1, R34.1, R38.2
HV2: JP23.3, R39.1
HV3: JP23.2, R40.1
HV-AC: JP23.5, R38.1
HV-HALL-SIGNAL: C101.1, JP22.2, R36.1
HV-PLUS: JP23.6, R41.2
HV_LEAK-: R2.1, R7.1, U$4.5 (+IN)
HV_LEAK_DIV+: R5.1, R41.1, U$4.3 (+IN)
JIC-INPUT: JP16.2, R20.2
JP17-PC4: JP17.1, R16.2
JP24-PC5: JP24.2, R100.2
L431-LED-GRN-CATHODE: LED3.C, R22.1
L431-LED-RED-CATHODE: LED4.C, R21.1
L431-PA13-SWDIO: JP15.3, STM32L1.46 (PA13)
L431-PA14-SWCLK: JP15.2, STM32L1.49 (PA14)
L431-PB0-LED-GRN: R22.2, STM32L1.26 (PB0)
L431-PB1-LED-RED: R21.2, STM32L1.27 (PB1)
L431-PC10-USART3-TX2: FET-SUB1.1 (G), STM32L1.51 (PC10)
L431-PC11-USART3-RX: OPT100.P$4 (OUT), R43.1, STM32L1.52 (PC11)
L431-UART-TX-FET: FET-SUB1.3 (D), R17.1
L431-USART-TX-OPTO: OPT2.P$2 (C), R17.2
L431-VDDA: BEAD1.2, C111.1, C114.1, R26.2, STM32L1.13 (VDDA)
L-I2C2-SDA: JP36.4, R27.1, STM32L1.34 (PB13)
L-PA5-SPI1-SCK: IC4.5 (I), STM32L1.21 (PA5)
L-PA6-SPI1-MISO: IC4.11 (O), STM32L1.22 (PA6)
L-PA7-SPI1-MOSI: IC4.2 (I), STM32L1.23 (PA7)
L-PB14-I2C2-SDA: JP36.3, R42.1, STM32L1.35 (PB14)
L-SPI1-MISO: IC4.12 (I), JP35.4
L-SPI1-MOSI: IC4.3 (O), JP35.3
L-SPI1-SCK: IC4.6 (O), JP35.2
LED-EXT-GRN-CATHODE: LED5.C, R23.1
LED-EXT-RED-CATHODE: LED6.C, R24.1
LED-EXT-RED-CATHODE2: LED2.C, R3.1
LED_BUS_PWR: LED1.C, R1.2
MASTER-RESET-RESISTOR: D102.C, OPT1.P$1 (A), R107.2
MASTER-RESET-SYS: D2.C, D102.A, JP3.8, JP4.8, JP5.8, JP6.8, OPT1.P$2 (C)
MASTER_RESET1: D2.A, D3.A, JP1.8, JP2.8
unnamed: D6.C, FET4.1 (G), JP14.2
NRST: OPT1.P$4 (OUT), R8.1, RESET0.1, RESET0.2, U1.7 (NRST)
NRST1: R25.2, RESET1.1, RESET1.2, STM32L1.7 (NRST)
PA0-T2C1: JP7.2, U1.14 (PA0)
PA1-T2C2|SYS12V: JP7.3, JP37.1, R46.1, R47.1, U1.15 (PA1)
PA2-USART2-TX: JP12.4, U1.16 (PA2)
PA3-USART2-RX: JP12.3, U1.17 (PA3)
PA4-RSP12V_POLARITY: R18.1, R44.1, U1.20 (PA4)
PA5-MASTER-RESET: FET1.1 (G), R6.1, U1.21 (PA5)
PA6: R110.1, R111.2, R112.1, U1.22 (PA6)
PA7-12V-PROTECT-DIVIDER: R14.1, R15.1, U1.23 (PA7)
PA8-HDRX3: IC3.12 (I), R147.1, U1.41 (PA8)
PA9-HDRX1: IC3.9 (I), R146.1, U1.42 (PA9)
PA9-USART1-TX: JP13.3, STM32L1.42 (PA9)
PA10-HDRX4: IC3.2 (I), R144.1, U1.43 (PA10)
PA10-USART1-RX: JP13.2, STM32L1.43 (PA10)
PA11-HDRX2: IC3.5 (I), R148.1, U1.44 (PA11)
PA12-KEYSW-SENSE: FET4.3 (D), U1.45 (PA12)
PA13-SWDIO: JP20.3, U1.46 (PA13)
PA14-SWCLK: JP20.2, U1.49 (PA14)
PA15-OPTO-OUT: OPT3.P$4 (OUT), R45.1, U1.50 (PA15)
PB0_HVLEAK+: U1.26 (PB0), U$4.1 (OUT), U$4.2 (-IN)
PB1-HV_LEAK-: U1.27 (PB1), U$4.6 (-IN), U$4.7 (OUT)
PB3-SUB9: FET-SUB104.1 (G), R-SUB100.1, U1.55 (PB3)
PB4: R20.1, R102.2, U1.56 (PB4)
PB5-CAN2-RX: IC1.4 (RXD), U1.57 (PB5)
PB6-CAN2-TX: IC1.1 (TXD), U1.58 (PB6)
PB8-CAN1-RX: IC102.4 (RXD), U1.61 (PB8)
PB9-CAN1-TX: IC102.1 (TXD), U1.62 (PB9)
PB11-I2C2-SDA|VCAP1: CP102.1, U1.30 (PB11)
PB12-LED2-GREEN: R23.2, U1.33 (PB12)
PB13-LED3-RED: R24.2, U1.34 (PB13)
PC0-ADC1_IN1: C3.1, R36.2, R101.1, STM32L1.8 (PC0)
PC0-IN10: C137.1, JP9.1, R12.2, U1.8 (PC0)
PC1-ADC1_IN2: C109.1, R31.1, R35.2, STM32L1.9 (PC1)
PC1-IN11: C140.1, JP8.1, R11.2, U1.9 (PC1)
PC2-ADC1-IN3: C108.1, R29.1, R32.2, STM32L1.10 (PC2)
PC2-IN12: C139.1, JP10.1, R10.2, U1.10 (PC2)
PC3-ADC1-IN4: C107.1, R28.1, R33.2, STM32L1.11 (PC3)
PC3-IN13: C138.1, JP11.1, R13.2, U1.11 (PC3)
PC4-ADC1_IN9: C106.1, R26.1, R30.1, R34.2, STM32L1.20 (PA4)
PC4-IN14: C133.1, R16.1, R118.2, R128.2, U1.24 (PC4)
PC5-IN15: C124.1, R19.2, R100.1, R119.2, U1.25 (PC5)
PC10-USART3-TX: JP18.3, U1.51 (PC10)
PC11-USART3-RX: JP18.2, U1.52 (PC11)
PC12-UART5-TX: FET3.1 (G), U1.53 (PC12)
PC13-NFET-GATE: FET2.1 (G), U1.2 (PC13)
PC14_OSC32IN|XTAL: C136.1, R113.1, U1.3 (PC14), UNK32KHZ0.2
PC15-32OSC-OUT: C141.1, R113.2, U1.4 (PC15), UNK32KHZ0.1
PD0_OSC_IN_XTAL: C143.1, Q100.2, R103.1, U1.5 (PD0/OSC<=)
PD1_OSC_OUT: C142.1, Q100.1, R103.2, U1.6 (PD1/OSC=>)
PD2-UART5-RX: OPT2.P$4 (OUT), R116.2, U1.54 (PD2)
PFET-SWITCH-GATE: D101.A, R105.1, R106.2, U$3.G
PFET-SWITCH-OR: D5.A, D6.A, R105.2
SUBH1-FET-GATE: FETS1.G, IC2.8 (O), RSG2.1
SUBH2-FET-GATE: FETS2.G, IC2.6 (O), RSG1.1
SUBH5-FET-GATE: FETS3.G, IC2.11 (O), RSG3.1
SUBH6-FET-GATE: FETS4.G, IC2.3 (O), RSG4.1
UART5-TX: OPT100.P$2 (C), R-SUB1.2
V+: BEAD1.1, C116.1, C117.1, C118.1, C125.1, C128.1, OPT100.P$6 (VCC), R25.1, R43.2, REG1A101.3 (VO), STM32L1.1 (VBAT), STM32L1.19 (VDD_4), STM32L1.32 (VDD_1), STM32L1.48 (VDD_2), STM32L1.64 (VDD_3)
VBAT: R9.1, R115.2, U1.1 (VBAT)
VCAN2: D1.A, JP3.2 (5), JP3.3 (2), JP4.2 (5), JP4.3 (2), JP5.2 (5), JP5.3 (2), JP6.2 (5), JP6.3 (2), R47.2
VCC: BEAD0.1, C121.1, C123.1, C126.1, C127.1, C129.1, C131.1, C135.1, CP103.1, LED5.A, LED6.A, OPT1.P$6 (VCC), OPT2.P$6 (VCC), R2.2, R8.2, R9.2, R10.1, R11.1, R12.1, R13.1, R19.1, R110.2, R116.1, R118.1, REG1A0.3 (VO), U1.19 (VDD_4), U1.32 (VDD_1), U1.48 (VDD_2), U1.64 (VDD_3), U$4.8 (VDD)
VDDA1: BEAD0.2, C130.1, U1.13 (VDDA)
VPP: +12SW0.G1, +12SW0.G2, D4.A, JP1.2 (5), JP1.3 (2), JP2.2 (5), JP2.3 (2), U$3.D
VSS_1-VCAP_1: CP100.1, U1.31 (VSS_1)
VSS_3: CP101.1, U1.47 (VSS_2)

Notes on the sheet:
PJQ4403
VDD by-pass
Minus
This could be
f405 = VCAP_1 2.2u
R37 if no coin
RED
a zener, or cap
DMP3007SCG-7
f446 = VCAP_1 2.2u
PTS647-1841803
Processor
SELECT TX
Master Reset
1217136-1
RESET
l431 = PB11
R100 zero R119 open for thermistor
Pressure
JIC input
5.0V
Power Pole
32768Hz
FET4 Vgs
R16 zero; R128 open for thermistor
TE Connectivity
CAN2
f446 = VSS zero ohm
CHANNEL 1
SYSTEM (CAN) GROUND
CP3
HARD
NOTE:
l431 = VSS zero ohm
CP2
CAN1
Pin 30
VCAP_2
MASTER RESET
R119 open for pressure

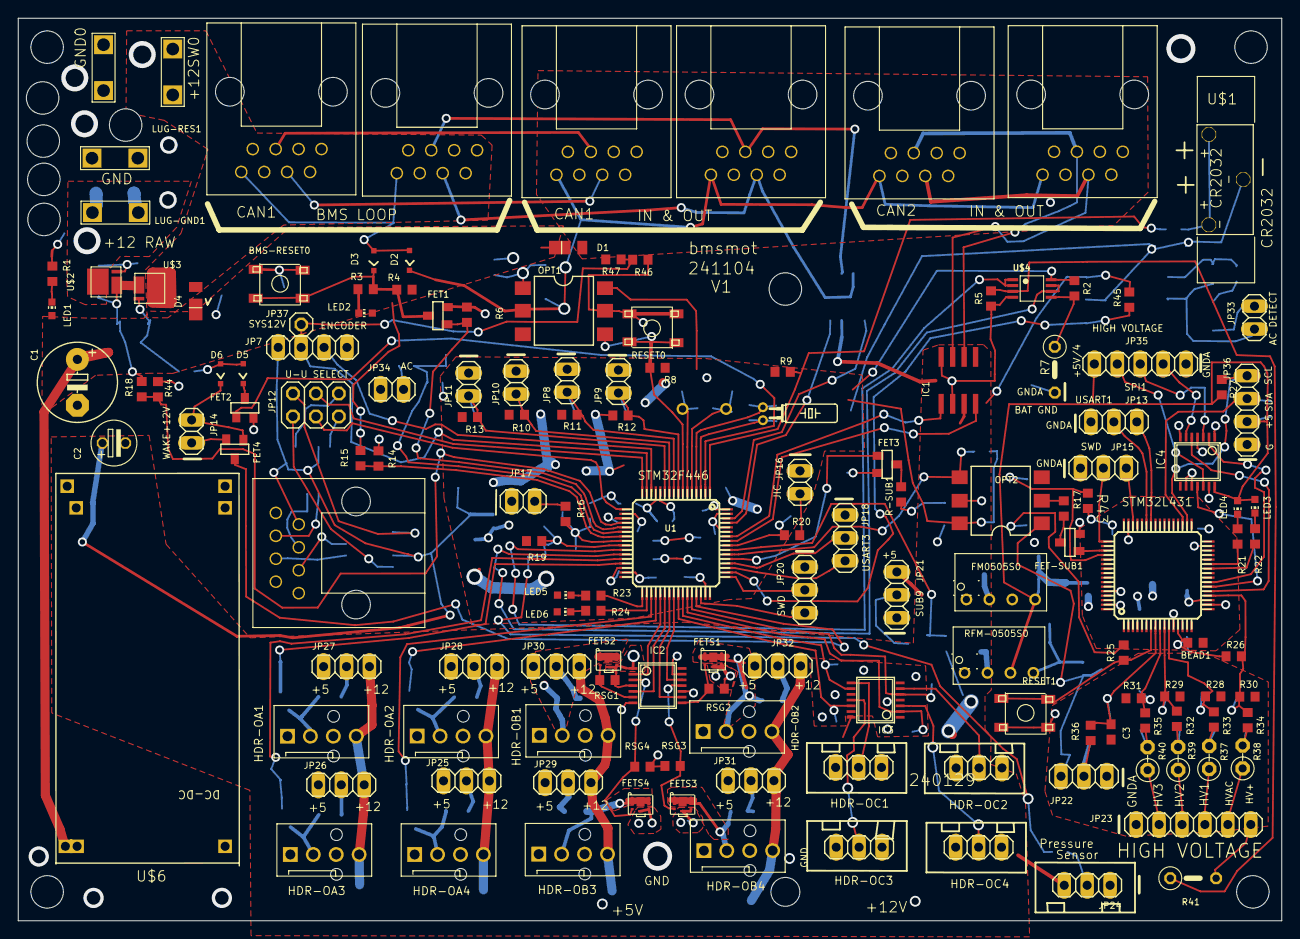
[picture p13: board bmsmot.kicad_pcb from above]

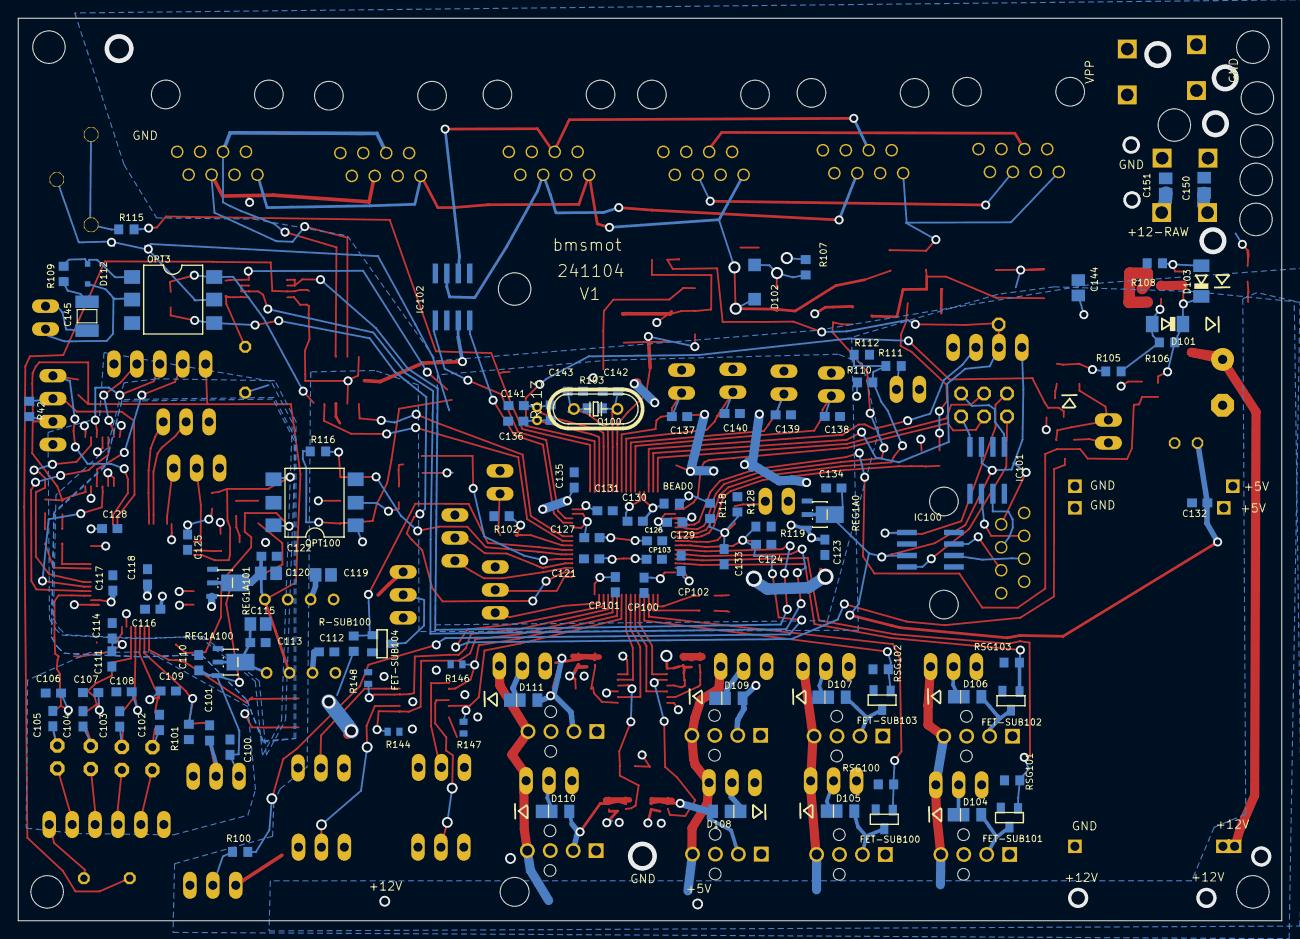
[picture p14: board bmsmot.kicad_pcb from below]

Board: 2 copper layers, 140.0 x 100.0 mm, 266 parts (107 on the bottom side), 170 nets.

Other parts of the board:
UNK_HOLE_0: dummyfp0
UNK_HOLE_1: dummyfp1
UNK_HOLE_2: dummyfp2
UNK_HOLE_3: dummyfp3
UNK_HOLE_4: dummyfp4
UNK_HOLE_5: dummyfp5
UNK_HOLE_6: dummyfp6
UNK_HOLE_7: dummyfp7
UNK_HOLE_8: dummyfp8
UNK_HOLE_9: dummyfp9
UNK_HOLE_10: dummyfp10

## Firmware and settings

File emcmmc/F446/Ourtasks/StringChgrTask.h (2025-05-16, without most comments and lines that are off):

#define __STRINGCHGRTASK
#include <stdint.h>
#include "FreeRTOS.h"
#include "cmsis_os.h"
#include "can_iface.h"
#include "GatewayTask.h"
#define MMCSTATUS_BMSSTAT  (1 << 0) // 1 = ALL BMS nodes reporting status
#define MMCSTATUS_BMSCELL  (1 << 1) // 1 = ALL BMS nodes reporting cell readings
#define MMCSTATUS_CHRGR    (1 << 2) // 1 = Charger reporting OK
#define MMCSTATUS_BMSLMITS (1 << 3) // 1 = All BMS nodes reported v & i limits
#define SCTSTATUS_EXP (1<<0) // Expected number is reporting
#define SCTSTATUS_OVF (1<<1) // Received more than table size
#define SCTSTATUS_FWR (1<<2) // Fewer than expected reporting
#define SCTSTATUS_MOR (1<<3) // More  than expected reporting
#define SCTSTATUS_NR  (1<<4) // Missing node readings, or not up-to-date
#define ELCONSTATUS_HWFAIL (1<<0) //  1 Hardware failure
#define ELCONSTATUS_OVTEMP (1<<1) //  2 Over temperature
#define ELCONSTATUS_INVOLT (1<<2) //  4 Input voltage wrong
#define ELCONSTATUS_DISCNT (1<<3) //  8 Battery disconnected
#define ELCONSTATUS_COMMTO (1<<4) // 10 Communications timeout
#define ELCONSTATUS_REPORT (1<<5) // 20 ELCON is reporting
#define ELCONSTATUS_TIMOUT (1<<6) // 40 Time out bits [0:4] not ready
#define CHGSTATUS_MODE  (1<<0) // 0 = relaxation; 1 = charging
#define CHGRATENUM 6 // Number of charger current steps
#define DEFAULT_VMAX ((3650*18)*0.1f) // (Voltage max 0.1v)
#define DEFAULT_IMAX (13) // Charging max (0.1a)
#define DEFULAT_IBAL (1)  // Balancing max (0.1a)
#define STRINGCHRGBIT00 (1<<0) // GatewayTask
#define STRINGCHRGBIT01 (1<<1) // RTOS timer swtim1
#define SWTIME1PERIOD 50 // 50 ms ticks
#define TIMCTR_ELCON_POLL  ( 900/SWTIME1PERIOD) // Time between ELCON polls (900 ms)
#define TIMCTR_TIMEOUT_BMS (1000/SWTIME1PERIOD) // Timecheck BMS responding. (1000 ms)
#define TIMCTR_ELCON_TIMOUT (15000/SWTIME1PERIOD) // ELCON fails ready status (15sec)
#define TIMCTR_RELAX (6) // Charging turned off wait for cell volts to settle
#define TIMCTR_ELCON_POLLFLAG (6000/SWTIME1PERIOD) // Wait to reset ELCON poll flag
#define TIMCTR_ELCON_RCV (2000/SWTIME1PERIOD) // Wait for ELCON response to poll
#define DISCOVERY_POLL_CT 6 // Allow 6 polls before ending discovery phase
#define EMCCMD_ELIDLE   0 // ELCON: Self discharging/stop
#define EMCCMD_ELCHG    1 // ELCON: Start charging
#define EMCCMD_LCCHG    2 // Node Low Current: set charging mode
#define EMCCMD_LCIDLE   3 // Node Low Current: self discharging/stop
#define EMCCMD_DBGSET   4 // Debug: ELCON: Force volts & amps setting
#define EMCCMD_POLLRATE 5 // Set BMS poll rate
#define BMSTABLESIZE 7 // Max size of table
#define BSTATUS_NOREADING (1 << 0)	// Exactly zero = no reading
#define BSTATUS_OPENWIRE  (1 << 1)  // Negative or over 5v indicative of open wire
#define BSTATUS_CELLTOOHI (1 << 2)  // One or more cells above max limit
#define BSTATUS_CELLTOOLO (1 << 3)  // One or more cells below min limit
#define BSTATUS_CELLBAL   (1 << 4)  // Cell balancing in progress
#define BSTATUS_CHARGING  (1 << 5)  // Charging in progress
#define BSTATUS_DUMPTOV   (1 << 6)  // Dump to a voltage in progress
#define FET_DUMP     (1 << 0) // 1 = DUMP FET ON
#define FET_HEATER   (1 << 1) // 1 = HEATER FET ON
#define FET_DUMP2    (1 << 2) // 1 = DUMP2 FET ON (external charger)
#define FET_CHGR     (1 << 3) // 1 = Charger FET enabled: Normal charge rate
#define FET_CHGR_VLC (1 << 4) // 1 = Charger FET enabled: Very Low Charge rate
#define MODE_CHRGING   (1 << 0) // 0 = Self discharge; 1 = charging
#define MODE_CHRGEND   (1 << 1) // 0 = Chrg ended; 1 = In progress
#define MODE_CELLTRIP  (1 << 2) // 1 = One or more cells tripped max
#define STSSTATE_IDLE   0  // Just poll ELCON to keep its COMM status alive
#define STSSTATE_CHRG   1  // Charging in progress
#define STSSTATE_RELAX  2  // Waiting for cells to relax after charge stopped.
#define STSSTATE_DBG    3  // PC or EMC direct setting of volts, amps, rate idx
#define STSSTATE_DISCOVERY 4 //
#define STS2_NODES_RPT  (1 << 0) // 1 = All discovered nodes reported status
struct BMSTABLE
{
	uint32_t id;        // Node CAN id
	uint32_t vsum;      // last complete (18 cells) sum of cells (100uv)
	uint32_t vsum_work; // summation from six CAN msgs in progress
	int32_t toctr_cell;   // Timeout counter: cell readings (0 = timed out)
	int32_t toctr_status; // Timeout counter: status (0 = timed out)
	uint16_t cell[18]; // Cell readings (100uv)
	uint16_t idxbits;  // Bit for 'idx' of six cell msgs (all on = 0x9249)
	uint16_t v_max;    // Voltage max for this module
	uint8_t i_max;     // Max charging current (255 = 25.5a or greater)
	uint8_t i_bal;     // Max balancing current (0.1 steps)
	uint8_t batt;       // Battery status
	uint8_t fet;        // FET status
	uint8_t mode;       // Mode status
	uint8_t temperature;// Temperature status (maybe not implemented)
	uint8_t groupnum;   // Six cell readings group number
};
struct ELCONSTUFF
{
	float fmsgvolts;         // ELCON reported: volts
	float fmsgamps;          // ELCON reported: amps
	int32_t toct_poll_dur;   // Timer tick ct for polling duration (might be variable)
	int32_t toctr_elcon_rcv; // Timeout counter: ELCON rcv msgs
	int32_t toctr_wait1;     // Timeout counter: delay 1
	int32_t toctr_wait2;     // Timeout counter: delay 2
	int32_t toctr_elcon_poll;// Timeout counter: ELCON poll
	int32_t toctr_elcon_ready; // Receving ELCON mgs, but status shows not ready
	int32_t toctr_elcon_pollflag; // Timeout counter: others sent a ELCON poll
	uint16_t ichgr_maxvolts; // Parameter float(volts) to uint32_t ui(0.1v)
	uint16_t ichgr_maxamps;  // Parameter float(amps) to uint32_t ui(0.1a)
	uint16_t ichgr_setvolts; // Set ELCON: (0.1v)
	uint16_t ichgr_setamps;  // Set ELCON: (0.1a)
	uint8_t status_elcon;    // uc[4] status byte rcvd from ELCON
	uint8_t pollflag;        // 0 = OK; 1 = someone else sent a poll CAN msg
	int8_t discovery_ctr; // Count ELCON timed BMS polls for discovery
};
struct STRINGCHGRFUNCTION
{
	struct ELCONSTUFF elconstuff; // Group ELCON vars together
	struct BMSTABLE bmstable[BMSTABLESIZE]; // Entry for each BMS node
	struct BMSTABLE* pbmstbl[BMSTABLESIZE]; // Ptrs for sorted sequence
	struct CANTXQMSG canelcon; // CAN msg for sending to ELCON
	struct CANTXQMSG canbms;   // CAN msg for sending to BMS nodes
	uint32_t hbct_t;   // Duration between STRINGCHGR function heartbeats(ms)
	uint32_t hbct_tic; // Loop tick count between heartbeats
	int32_t  hbct_ctr; // Heartbeat time count-down
	int32_t toctr_relax; // Wait after turning off ELCON
	float chgr_maxvolts; // Set charger voltage limit (volts)
	float chgr_maxamps;  // Set charger current limit (amps)
	float chgr_balamps;  // Balancing current limit (amps)
	uint16_t vi_max_rpt; // Bits that module reported V & I max limits
	float chgr_rate[CHGRATENUM]; // Amps
	uint8_t bmsnum_expected; // Number of BMS nodes expected to be reporting
	uint8_t bmsnum;    // Discovered number of BMS nodes.
	 int8_t chgr_rate_idx; // Index of rate in effect.
	uint8_t nodeok; // Bits for each node that all readings received from poll
	int8_t remap[BMSNODEIDSZ];
	uint8_t status1;   // Bits on BMS number reporting
	uint8_t mode;      // Charging or off
	uint8_t cellrcv;   // Node bits: all cell readings received
	uint8_t statusrcv; // Node bits: status msg received
	uint8_t statusmax; // Node bits: Cell above max in status report
	uint8_t status2;   // ?
	uint8_t stsstate;  // Charging management state
	uint8_t cmdpendingidle;
	uint8_t cmdpendingchg;
	uint8_t cmdpendingchg_prev;
};
 TaskHandle_t xStringChgrTaskCreate(uint32_t taskpriority);
extern TaskHandle_t StringChgrTaskHandle;

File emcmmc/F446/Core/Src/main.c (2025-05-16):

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
/* Includes ------------------------------------------------------------------*/
#include "main.h"
#include "cmsis_os.h"

/* USER CODE BEGIN Includes */
#include <string.h>
#include "morse.h"
#include "DTW_counter.h"
#include <math.h>

#include "adcparams.h"
#include "SerialTaskSend.h"
#include "SerialTaskReceive.h"
#include "CanTask.h"
#include "can_iface.h"
#include "canfilter_setup.h"
#include "getserialbuf.h"
#include "yprintf.h"
#include "ADCTask.h"
#include "MailboxTask.h"
#include "CanCommTask.h"
#include "CoolingTask.h"
#include "rtcregs.h"
#include "EMCLTask.h"
#include "RyTask.h"
#include "emcl_idx_v_struct.h"
#include "iir_f1.h"
#include "StringChgrTask.h"
#include "stringchgr_items.h"
#include "GatewayTask.h"
#include "DMOCTask.h"
#include "ContactorTask.h"

#include "FreeRTOS.h"
#include "semphr.h"
/* USER CODE END Includes */

/* USER CODE BEGIN PTD */
uint32_t timectr = 0;
struct CAN_CTLBLOCK* pctl0; // Pointer to CAN1 control block
struct CAN_CTLBLOCK* pctl1; // Pointer to CAN2 control block

uint32_t debugTX1b;
uint32_t debugTX1b_prev;

uint32_t debugTX1c;
uint32_t debugTX1c_prev;

uint32_t debug03;
uint32_t debug03_prev;

//extern osThreadId SerialTaskHandle;
//extern osThreadId CanTxTaskHandle;
//extern osThreadId CanRxTaskHandle;
//extern osThreadId SerialTaskReceiveHandle;

uint16_t m_trap = 450; // Trap codes for MX Init() and Error Handler

uint8_t canflag;
uint8_t canflag1;
//uint8_t canflag2;

int8_t rtcregs_ret; // RTC register init return

//const uint32_t i_am_canid = I_AM_CANID;

/* USER CODE END PTD */

/* USER CODE BEGIN PM */
  /* 
  Timer usage
                         1    2   3   4   auto  auto
  TIM1 charger control  PWM   x   x   x  comp1 comp2
                        PA8               PA6   PA11 
  TIM2 FAN PWM TACH     PWM   x  IC   x    
                        PA5     PB10
  TIM7  System          x     

  TIM15 SPI/ADC/BMS     OC    x
  
  */
/* USER CODE END PM */

ADC_HandleTypeDef hadc1;
ADC_HandleTypeDef hadc2;
DMA_HandleTypeDef hdma_adc1;
DMA_HandleTypeDef hdma_adc2;

CAN_HandleTypeDef hcan1;
CAN_HandleTypeDef hcan2;

TIM_HandleTypeDef htim1;
TIM_HandleTypeDef htim2;
TIM_HandleTypeDef htim3;
TIM_HandleTypeDef htim5;
TIM_HandleTypeDef htim9;
TIM_HandleTypeDef htim12;
TIM_HandleTypeDef htim13;

UART_HandleTypeDef huart5;
UART_HandleTypeDef huart2;
UART_HandleTypeDef huart3;
DMA_HandleTypeDef hdma_uart5_rx;
DMA_HandleTypeDef hdma_usart2_tx;
DMA_HandleTypeDef hdma_usart2_rx;
DMA_HandleTypeDef hdma_usart3_rx;
DMA_HandleTypeDef hdma_usart3_tx;

DMA_HandleTypeDef hdma_memtomem_dma2_stream1;
osThreadId defaultTaskHandle;
/* USER CODE BEGIN PV */
uint16_t errorcode;
/* USER CODE END PV */

void SystemClock_Config(void);
static void MX_GPIO_Init(void);
static void MX_DMA_Init(void);
static void MX_CAN1_Init(void);
static void MX_CAN2_Init(void);
static void MX_UART5_Init(void);
static void MX_USART2_UART_Init(void);
static void MX_USART3_UART_Init(void);
static void MX_TIM1_Init(void);
static void MX_TIM2_Init(void);
static void MX_ADC1_Init(void);
static void MX_TIM3_Init(void);
static void MX_TIM12_Init(void);
static void MX_TIM5_Init(void);
static void MX_TIM13_Init(void);
static void MX_TIM9_Init(void);
static void MX_ADC2_Init(void);
void StartDefaultTask(void const * argument);

/**
  * @brief  The application entry point.
  * @retval int
  */
int main(void)
{
  /* USER CODE BEGIN 1 */
  BaseType_t ret;    // Used for returns from function calls
  osThreadId Thrdret;  // Return from thread create
  /* USER CODE END 1 */

  /* MCU Configuration--------------------------------------------------------*/

  /* Reset of all peripherals, Initializes the Flash interface and the Systick. */
  HAL_Init();

  /* USER CODE BEGIN Init */
  DTW_counter_init();
  /* USER CODE END Init */

  /* Configure the system clock */
  SystemClock_Config();

  /* Initialize all configured peripherals */
  MX_GPIO_Init();
  MX_DMA_Init();
  MX_CAN1_Init();
  MX_CAN2_Init();
  MX_UART5_Init();
  MX_USART2_UART_Init();
  MX_USART3_UART_Init();
  MX_TIM1_Init();
  MX_TIM2_Init();
  MX_ADC1_Init();
  MX_TIM3_Init();
  MX_TIM12_Init();
  MX_TIM5_Init();
  MX_TIM13_Init();
  MX_TIM9_Init();
  MX_ADC2_Init();
  /* USER CODE BEGIN 2 */
  /* CAN ID for this node is passed in to make from command line. */
//  i_am_canid = I_AM_CANID;

  /* USER CODE END 2 */

  /* USER CODE BEGIN RTOS_MUTEX */
  /* add mutexes, ... */
  /* USER CODE END RTOS_MUTEX */

  /* USER CODE BEGIN RTOS_SEMAPHORES */
  /* add semaphores, ... */
  #define NUMCIRBCB1  16 // Size of circular buffer of BCB for usart3
  ret = xSerialTaskSendAdd(&HUARTMON, NUMCIRBCB1, 1); // dma
  if (ret < 0) morse_trap(111); // Panic LED flashing
  
  yprintf_init();
  /* USER CODE END RTOS_SEMAPHORES */

  /* USER CODE BEGIN RTOS_TIMERS */
  /* start timers, add new ones, ... */

  //morse_trap(333);
  //HAL_GPIO_WritePin(GPIOB, GPIO_PIN_12, GPIO_PIN_RESET);
  //while(1==1);
  /* USER CODE END RTOS_TIMERS */

  /* USER CODE BEGIN RTOS_QUEUES */
  /* add queues, ... */
  /* USER CODE END RTOS_QUEUES */

  /* Create the thread(s) */
  /* definition and creation of defaultTask */
  osThreadDef(defaultTask, StartDefaultTask, osPriorityNormal, 0, 448);
  defaultTaskHandle = osThreadCreate(osThread(defaultTask), NULL);

  /* USER CODE BEGIN RTOS_THREADS */
  /* add threads, ... */

/* Relay/output handler. */
  //ry_init(); // Task does this
  TaskHandle_t rett = xRyTaskCreate(osPriorityNormal);
  if (rett == NULL) morse_trap(109);

  Thrdret = xADCTaskCreate(osPriorityNormal+2); // (arg) = priority
  if (Thrdret == NULL) morse_trap(117);

/* Create serial task (priority) */
  Thrdret = xSerialTaskSendCreate(osPriorityNormal); // Create task and set Task priority
  if (Thrdret == NULL) morse_trap(112);

  /* Add bcb circular buffer to SerialTaskSend for usart3 -- PC monitor */
  #define NUMCIRBCB3  16 // Size of circular buffer of BCB for usart3
  ret = xSerialTaskSendAdd(&HUARTMON, NUMCIRBCB3, 1); // dma
  if (ret < 0) morse_trap(14); // Panic LED flashing

  /* Setup TX linked list for CAN  */
   // CAN1 (CAN_HandleTypeDef *phcan, uint8_t canidx, uint16_t numtx, uint16_t numrx);
  pctl0 = can_iface_init(&hcan1, 0, 64, 32);       
  if (pctl0 == NULL) morse_trap(118); // Panic LED flashing
  if (pctl0->ret < 0) morse_trap(119);

#ifdef CONFIGCAN2
  pctl1 = can_iface_init(&hcan2, 1,32, 64);
  if (pctl1 == NULL) morse_trap(8); // Panic LED flashing
  if (pctl1->ret < 0) morse_trap(88);  
#endif

  /* Setup CAN hardware filters to default to accept all ids. */
  HAL_StatusTypeDef Cret;
  Cret = canfilter_setup_first(1, &hcan1, 15); // CAN1
  if (Cret == HAL_ERROR) morse_trap(219);

#ifdef CONFIGCAN2
  Cret = canfilter_setup_first(2, &hcan2, 15); // CAN2
  if (Cret == HAL_ERROR) morse_trap(217);
#endif  

/* Create CanTxTask - CAN driver TX interface. */
  // CanTask priority, Number of msgs in queue
  QueueHandle_t QHret = xCanTxTaskCreate(osPriorityNormal+1, 48); 
  if (QHret == NULL) morse_trap(120); // Panic LED flashing

  /* definition and creation of CanRxTask - CAN driver RX interface. */
  /* The MailboxTask takes care of the CANRx                         */
//  Qidret = xCanRxTaskCreate(1, 32); // CanTask priority, Number of msgs in queue
//  if (Qidret < 0) morse_trap(6); // Panic LED flashing

/* Create MailboxTask */
  xMailboxTaskCreate(osPriorityNormal+1); // (arg) = priority

/* Create Mailbox control block w 'take' pointer for each CAN module. */
  struct MAILBOXCANNUM* pmbxret;
  // (CAN1 control block pointer, size of circular buffer)
  pmbxret = MailboxTask_add_CANlist(pctl0, 32);
  if (pmbxret == NULL) morse_trap(215);

#ifdef CONFIGCAN2
    pmbxret = MailboxTask_add_CANlist(pctl1, 32);
    if (pmbxret == NULL) morse_trap(215);
#endif    

/* Create GatewayTask */
  xGatewayTaskCreate(osPriorityNormal); // (arg) = priority  

/* Create serial receiving task. */
  ret = xSerialTaskReceiveCreate(osPriorityNormal);
  if (ret != pdPASS) morse_trap(113);

/* Create EMCLTask */
  Thrdret = xEMCLTaskCreate(osPriorityNormal);
  if (Thrdret == NULL) morse_trap(108);

  /* Initialize hard-code params for functions. */
  emcl_idx_v_struct_hardcode_params(&emclfunction.lc);

/* Create CoolingTask */
  Thrdret = xCoolingTaskCreate(osPriorityNormal);
  if (Thrdret == NULL) morse_trap(110);

/* Create String Charging Task. */  
  Thrdret = xStringChgrTaskCreate(osPriorityNormal);
  if (Thrdret == NULL) morse_trap(114);

/* Create DMOC task. */
  Thrdret = xDMOCTaskCreate(osPriorityNormal);
  if (Thrdret == NULL) morse_trap(116);

/* Create Contactor Task. */
  Thrdret = xContactorTaskCreate(osPriorityNormal);
  if (Thrdret == NULL) morse_trap(122);

/* Create CAN communication task handler. */
  rett = xCanCommCreate(osPriorityNormal+2);
  if (rett == NULL) morse_trap(121);

  /* Select interrupts for CAN1 */
  HAL_CAN_ActivateNotification(&hcan1, \
    CAN_IT_TX_MAILBOX_EMPTY     |  \
    CAN_IT_RX_FIFO0_MSG_PENDING |  \
    CAN_IT_RX_FIFO1_MSG_PENDING    );

#ifdef CONFIGCAN2
/* Select interrupts for CAN2 */
  HAL_CAN_ActivateNotification(&hcan2, \
    CAN_IT_TX_MAILBOX_EMPTY     |  \
    CAN_IT_RX_FIFO0_MSG_PENDING |  \
    CAN_IT_RX_FIFO1_MSG_PENDING    );
#endif  

  /* USER CODE END RTOS_THREADS */

  /* Start scheduler */
  osKernelStart();

  /* We should never get here as control is now taken by the scheduler */
  /* Infinite loop */
  /* USER CODE BEGIN WHILE */
  while (1)
  {
    /* USER CODE END WHILE */

    /* USER CODE BEGIN 3 */
  }
  /* USER CODE END 3 */
}

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
/* USER CODE BEGIN Header_StartDefaultTask */
/**
  * @brief  Function implementing the defaultTask thread.
  * @param  argument: Not used
  * @retval None
  */


/* USER CODE END Header_StartDefaultTask */
void StartDefaultTask(void const * argument)
{
  /* USER CODE BEGIN 5 */
  
  struct SERIALSENDTASKBCB* pbuf1 = getserialbuf(&HUARTMON,144);
  if (pbuf1 == NULL) morse_trap(115);
  struct SERIALSENDTASKBCB* pbuf2 = getserialbuf(&HUARTMON,128);
  if (pbuf2 == NULL) morse_trap(125);
struct SERIALSENDTASKBCB* pbuf3 = getserialbuf(&HUARTMON,64);
  if (pbuf3 == NULL) morse_trap(125);
//struct SERIALSENDTASKBCB* pbuf4 = getserialbuf(&HUARTMON,64);
//if (pbuf4 == NULL) morse_trap(125);
HAL_GPIO_WritePin(GPIOB, GPIO_PIN_13, GPIO_PIN_RESET); // RED ON
osDelay(20);
  yprintf(&pbuf1,"\n\n\rPROGRAM STARTS\n\r");
HAL_GPIO_WritePin(GPIOB, GPIO_PIN_13, GPIO_PIN_SET); // RED OFF
  
//    qret=xQueueSendToBack(RyTaskReadReqQHandle, &rytest[j].preq, portMAX_DELAY);
//    if (qret == errQUEUE_FULL) morse_trap(123);  
//uint32_t ctr =0;
  /* Infinite loop */
  for(;;)
  {   

#if 0    
  extern uint32_t dbgcool1;
    yprintf(&pbuf1,"%5d\n\r", dbgcool1);
#endif

#if 1 // Green LED winking
    HAL_GPIO_WritePin(GPIOB, GPIO_PIN_12, GPIO_PIN_RESET); // GRN ON
        osDelay(3);
    HAL_GPIO_WritePin(GPIOB, GPIO_PIN_12, GPIO_PIN_SET); // GRN OFF
      osDelay(250-3);
#else
  static uint32_t yyctr;
  yprintf(&pbuf2,"%5d ",yyctr++);
  osDelay(1001);
#endif

#if 1
  static uint32_t sctr;
//  extern uint8_t do_bms_status_flag;
  extern uint8_t polltim_flag;
  struct STRINGCHGRFUNCTION* ps= &emclfunction.lc.lcstring;
  struct ELCONSTUFF* pe = &ps->elconstuff;    
  extern uint16_t pccmd;
//  if (do_bms_status_flag != 0)
  if (polltim_flag != 0)    
  {
    yprintf(&pbuf1,"%5d, statusmax %02x pccmd %04X ",sctr++,ps->statusmax,pccmd);
    yprintf(&pbuf2,"ststate %d discovery_ctr %d\n\r",ps->stsstate);
//    do_bms_status_flag = 0;
    polltim_flag = 0;
  }

extern uint8_t dbg_do_elcon_poll_flag;
extern uint8_t dbg_do_elcon_poll_status_elcon;
extern int32_t dbg_do_elcon_poll_toctr_elcon_rcv;
  if (dbg_do_elcon_poll_flag > 0)
  {
    yprintf(&pbuf1,"elcon_poll_flag %d  status_elcon %02X toctr_elcon_rcv %d",
      dbg_do_elcon_poll_flag,dbg_do_elcon_poll_status_elcon,dbg_do_elcon_poll_toctr_elcon_rcv);
    dbg_do_elcon_poll_flag = 0;
extern int32_t dbg_amps;
    yprintf(&pbuf3," ichgr_setvolts %d ichgr_maxamps %d dbg_amps %d\n\r",pe->ichgr_setvolts,pe->ichgr_maxamps,dbg_amps);
    yprintf(&pbuf2," chgr_rate_idx %d",ps->chgr_rate_idx);

    /* BMS status: CELLTOOHI for discovered nodes */
    char ln[12];
    char* pln = &ln[0];
    *pln++ = '|';
    for (int n = 0; n < ps->bmsnum; n++)
    { 
      if ((ps->pbmstbl[n]->batt & BSTATUS_CELLTOOHI) != 0)
        *pln = 'X';
      else
        *pln = '.';
      pln +=1;
    }
    *pln++ = '|'; *pln = 0;
extern int32_t toctr_relax;
    yprintf(&pbuf1," TOOHI %s statusmax %02X toctr_relax %d bmsnum %d\n\r",ln,ps->statusmax,ps->toctr_relax,ps->bmsnum);
  }

#endif   

#if 1 // BMS Discovery table data
    struct STRINGCHGRFUNCTION* ps2= &emclfunction.lc.lcstring;
extern uint8_t discovery_end_flag; // Signal main for printf'ing
  if (discovery_end_flag != 0)
  {
    discovery_end_flag = 0;
    yprintf(&pbuf1,"\n\rDiscovery END: Sorted Table----------------\n\r");
    yprintf(&pbuf2,"           v_max i_max i_bal\n\r");
    for (int n = 0; n < ps2->bmsnum; n++)
    {
      yprintf(&pbuf3,"%d %08X %5d %5d %5d\n\r", (n+1),ps->pbmstbl[n]->id,ps->pbmstbl[n]->v_max,ps->pbmstbl[n]->i_max, ps->pbmstbl[n]->i_bal );
    }
  yprintf(&pbuf1,"MAX: %12.1f %4.1f %5.1f\n\r\n\r",ps->chgr_maxvolts,ps->chgr_maxamps,ps->chgr_balamps);
  }

#endif  

#if 0
static uint32_t yyctr;
  static uint8_t bmsnum_prev;
  float fmsum;
  float totalv;
  yprintf(&pbuf1,"bmsnum %d\n\r",emclfunction.lc.lcstring.bmsnum);
  /* Output table when there is a change in size,
     OR, every 10 cycles. */
  if ((bmsnum_prev != emclfunction.lc.lcstring.bmsnum) || 
      ((yyctr % 10) == 0)      )
  { 
    bmsnum_prev = emclfunction.lc.lcstring.bmsnum;
    totalv = 0;
    for (int j = 0; j < emclfunction.lc.lcstring.bmsnum; j++)
    {
      yprintf(&pbuf2,"%2d %08X",j,emclfunction.lc.lcstring.pbmstbl[j]->id);

      // Sum cell readings for =>module<=
      uint32_t msum = 0;
      for (int k = 0; k < 18; k++)
      {
        msum += emclfunction.lc.lcstring.pbmstbl[j]->cell[k];
      }
      fmsum = msum;

      // Display
      if (emclfunction.lc.lcstring.pbmstbl[j]->toctr_cell > 0)
      { // Timeout counter for cell readings has not expired
        yprintf(&pbuf1," %6.3f",fmsum*0.0001f);
        for (int k = 0; k < 18; k++)
        { // Print individual cell readings (100uV)
          yprintf(&pbuf2," %4d",emclfunction.lc.lcstring.pbmstbl[j]->cell[k]);
        }
      }
      else
      { // Timeout expired, so readings are "stale"
        yprintf(&pbuf1," %6.3f",fmsum*0.0001f);
        for (int k = 0; k < 18; k++)
        { // Print individual cell readings (100uV)
          yprintf(&pbuf2,"_stale");
        }  
      }
      // Check gateway_items summation
      yprintf(&pbuf2,"\n\r      vsum %7.3f\n\r",emclfunction.lc.lcstring.pbmstbl[j]->vsum*0.0001f);
      totalv += fmsum; // Sum total battery string volts
    }
    yprintf(&pbuf1,"     total %7.3f\n\r",totalv*0.0001f);

  }
#endif  




#if 0    
  static uint32_t yctr;      
//  yprintf(&pbuf2,"%5d", yctr++);
  struct MOTORRAMP* pmr; //
   yprintf(&pbuf2,"%5d",yctr++);
  for (int k = 0; k < 4; k++)
// int k = 2; // Motor index (0-3) to be monitored
  {
    pmr = &emclfunction.lc.lccool.motorramp[k]; // Working struct
    yprintf(&pbuf1,":%2d %2d %4.1f %3d",pmr->state, pmr->target, 
      pmr->frampaccum,pmr->irampaccum);
  }
  yprintf(&pbuf2,"\n\r");
#endif

#if 0 // pwm testing
static struct RYREQ_Q ryreq_q1;
static struct RYREQ_Q* pryreqpssb;
static uint8_t ryreqinit;
static uint8_t ryrequpdn;
if (ryreqinit == 0)
{
  #define PWMSTEPUP 2 // If zero no remains at initial
  #define PWMSTEPDN 1 // 
  #define PWMMIN 5// Initial and slewing low limit
  #define PWMMAX 70 // Slewing high limit
  ryreqinit = 1;
  ryreq_q1.idx = 10; 
  ryreq_q1.pwm = PWMMIN; // Initial PWM
  ryreq_q1.cancel  = 0;
  pryreqpssb = &ryreq_q1;

}
if (ryrequpdn == 0)
{ // Here, Increase PWM
  ryreq_q1.pwm += PWMSTEPUP;
  if (ryreq_q1.pwm >= PWMMAX)
  {
    ryrequpdn = 1;
    ryreq_q1.pwm = PWMMAX;
  }
}
else
{ // Here Decrease PWM
  ryreq_q1.pwm -= PWMSTEPDN;

  if ((int8_t)ryreq_q1.pwm <= PWMMIN)
  {
    ryrequpdn = 0;
  }
}
xQueueSendToBack(RyTaskReadReqQHandle,&pryreqpssb,10000);
yprintf(&pbuf1,"PWM: %4d\n\r",ryreq_q1.pwm);

#endif      

#if 0
static uint32_t ctr;      
if (ctr == 0)
{
  yprintf(&pbuf1,"ADC1IDX_THERMISTOR1   0 PC0 IN10   JP9  Thermistor\n\r");
  yprintf(&pbuf1,"ADC1IDX_THERMISTOR2   1 PC1 IN11   JP8  Thermistor\n\r");
  yprintf(&pbuf1,"ADC1IDX_THERMISTOR3   2 PC2 IN12   JP10 Thermistor\n\r");
  yprintf(&pbuf1,"ADC1IDX_THERMISTOR4   3 PC3 IN13   JP11 Thermistor\n\r");
  yprintf(&pbuf1,"ADC1IDX_DIVIDEDSPARE  4 PC4 IN14   JP17 Spare: 10k|10k divider\n\r");
  yprintf(&pbuf1,"ADC1IDX_PRESS_SENSE   5 PC5 IN15   JP24 Pressure sensor\n\r");
  yprintf(&pbuf1,"ADC1IDX_12V_POWR      6 PA7 IN7    12v Power supply\n\r");
  yprintf(&pbuf1,"ADC1IDX_BATTLEAK_P    7 PB0 IN8    Battery string plus leakage\n\r");
  yprintf(&pbuf1,"ADC1IDX_BATTLEAK_M    8 PB1 IN9    Battery string minus leakage\n\r");
  yprintf(&pbuf1,"ADC1IDX_12V_POWR_DUP  6 PA7 IN7    12v Power supply (duplicate)\n\r");
  yprintf(&pbuf1,"ADC1IDX_INTERNALVBAT 10 IN18       VBAT\n\r");
  yprintf(&pbuf1,"ADC1IDX_INTERNALVREF 11 IN17       VREF\n\r");
  for(int j = 0; j < ADC1DIRECTMAX; j++)
    yprintf(&pbuf2,"        %2d",j);
  yprintf(&pbuf1,"\n\r");
}
ctr += 1;
if (ctr >= 32) ctr = 0;
{
 #if 1 // List calibrated & filtered.
  for(int j = 0; j < ADC1DIRECTMAX; j++)
  {
    yprintf(&pbuf2," %9.3f",adc1.abs[j].filt);
  }
  yprintf(&pbuf1,"\n\r");
 #endif

extern struct CANRCVBUF cooltest; 
extern uint8_t cooltest1;
  if (cooltest1 != 0)
  {
    cooltest1 = 0;
    yprintf(&pbuf1,"\n\r 0x%08X",cooltest.id);
  }

 #if 0 // List ADC sum (use for calibration)
 extern uint32_t dbg_adcsum[ADC1DIRECTMAX];
 static struct FILTERIIRF1 iiradcsum[ADC1DIRECTMAX]; // iir_f1 (float) filter
 static float fsumsum;
 static uint8_t dbgflag;
 if (dbgflag == 0)
 {
  // OTO initilization
  for(int j = 0; j < ADC1DIRECTMAX; j++)
  {
    iiradcsum[j].skipctr  = 4;
    iiradcsum[j].coef     = 0.95f;
    iiradcsum[j].onemcoef = 1 - iiradcsum[j].coef;  
  }
  dbgflag = 1;
 }
  for(int j = 0; j < ADC1DIRECTMAX; j++)
  {
    float ftmp = dbg_adcsum[j];
    fsumsum = iir_f1_f(&iiradcsum[j], ftmp);
    yprintf(&pbuf2," %9.1f",fsumsum);
//    yprintf(&pbuf2," %9d",dbg_adcsum[j]);
  }
  yprintf(&pbuf1,"\n\r");
 #endif
}
#endif

#if 0 // 60 Hz output ac measurement
float fnum;
float facc;
float fsmq;
float frecip;
float filtoffset;
struct ADC2NUM* pnum = get_adc2num();
/* Setup pbuf1 while pbuf2 sends */
if (pnum == NULL)
{
  HAL_GPIO_WritePin(GPIOB, GPIO_PIN_12, GPIO_PIN_RESET); // GRN ON 
}
else
{
  fnum = pnum->ctr;
  facc = pnum->acc;
  fsmq = pnum->smq;
  frecip = 1.0/fnum;
  facc = facc * frecip;
  fsmq = sqrtf(fsmq * frecip) * adc1.lc.adc2offset_scale;
  filtoffset = iir_f1_f(&adc1.lc.iir_adc2offset, facc);
  yprintf(&pbuf2,"\n\r%2d %8.2f  %8.2f %8.3f",ctr, facc,filtoffset,fsmq);
  ctr += 1; if (ctr >= 60) ctr = 0;
  HAL_GPIO_WritePin(GPIOB, GPIO_PIN_12, GPIO_PIN_SET); // GRN OFF
}
/* Setup pbuf2 while pbuf1 sends */
pnum = get_adc2num();
if (pnum == NULL)
{
  HAL_GPIO_WritePin(GPIOB, GPIO_PIN_12, GPIO_PIN_RESET); // GRN ON 
}
else
{
  fnum = pnum->ctr;
  facc = pnum->acc;
  fsmq = pnum->smq;
  frecip = 1.0/fnum;
  facc = facc * frecip;
  fsmq = sqrtf(fsmq * frecip) * adc1.lc.adc2offset_scale;
  filtoffset = iir_f1_f(&adc1.lc.iir_adc2offset, facc);
  yprintf(&pbuf2,"\n\r%2d %8.2f  %8.2f %8.3f",ctr, facc,filtoffset,fsmq);
  ctr += 1; if (ctr >= 60) ctr = 0;
  HAL_GPIO_WritePin(GPIOB, GPIO_PIN_12, GPIO_PIN_SET); // GRN OFF
}
osDelay(20); // Do not hog all the time.
#endif


#if 0 // Display (large) buffer of raw ADC2 readings
#ifdef MEMTOMEMCOPY // Uncomment in ADCTask.h
#define DEBUGSZ (ADC2SEQNUM*32)
extern uint32_t debugadcsumidx;
extern uint16_t debugadcsum[];
extern uint16_t debugexti[];
      if (debugadcsumidx >= DEBUGSZ)
      {
        ctr = 0;
        for (int j = 0; j < DEBUGSZ; j++)
        {
          yprintf(&pbuf1,"\n\r%5d %9d",ctr++,debugadcsum[j], debugexti[j]);
          if (debugexti[j] != 0)
            yprintf(&pbuf2," %6d",debugexti[j]);
        }
        HAL_GPIO_WritePin(GPIOB, GPIO_PIN_12, GPIO_PIN_SET); // GRN OFF
extern uint32_t debugdmamm2;
extern uint32_t debugdmakk2;
yprintf(&pbuf1,"\n\rm-m: %d inline: %d\n\r",debugdmamm2,debugdmakk2);
        osDelay(1000*6);
        debugadcsumidx = 0;
        ctr = 0;
      }
      else
      {
//          yprintf(&pbuf1,"\n\r%5d %9d",ctr++,debugadcsumidx);
      }
#endif
#endif


#if 0 // Display time between EXTI interrupts (60 Hz)
extern uint32_t exti15dtw_diff;
extern uint32_t  exti15dtw_flag;
extern uint32_t  exti15dtw_flag_prev;

extern uint32_t exti15dtw_accum_flag;
extern int32_t  exti15dtw_accum_diff;
if (exti15dtw_accum_flag != 0)
{
      yprintf(&pbuf1,"\n\r%9d %8d %8d",ctr++,exti15dtw_diff,exti15dtw_diff/180);
        exti15dtw_flag_prev = exti15dtw_flag;
}        
//extern uint32_t exti15dtw_irqctr;
      //yprintf(&pbuf2," %8d",exti15dtw_irqctr);

extern uint32_t exti15dtw_reg; 
extern uint32_t debugadc2dma_pdma2;
extern uint32_t adc2dma_cnt;
//        yprintf(&pbuf2," Reg: 0x%08X %7d %7d",adc2dma_cnt,debugadc2dma_pdma2,exti15dtw_reg);
//extern exti15dtw_reg1;
//      yprintf(&pbuf1," %d",exti15dtw_reg1);
#endif

#if 0
extern uint32_t exti15dtw_accum_flag;
extern int32_t  exti15dtw_accum_diff;
if (exti15dtw_accum_flag != 0)
{
  exti15dtw_accum_flag = 0;
  float faccum = (exti15dtw_accum_diff/240);
  faccum = (faccum /180.0f);
  yprintf(&pbuf1," %7d %10.1f %10.4f%% %10.3f",(exti15dtw_accum_diff/240),faccum,100.0f*((1E6f/60.0f)/faccum - 1.0f),(1E6f/faccum));
}
#endif
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

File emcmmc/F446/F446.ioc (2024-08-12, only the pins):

Mcu.UserName=STM32F446RETx
PA10.GPIO_Label=OC4
PA10.Signal=S_TIM1_CH3
PA11.GPIO_Label=OC2
PA11.Signal=S_TIM1_CH4
PA12.GPIO_Label=Keyswsense
PA12.Signal=GPIO_Input
PA13.Signal=SYS_JTMS-SWDIO
PA14.Signal=SYS_JTCK-SWCLK
PA15.GPIO_Label=ACzeroxing
PA15.Signal=GPXTI15
PA2.Signal=USART2_TX
PA3.Signal=USART2_RX
PA5.GPIO_Label=M-RESET
PA5.Signal=GPIO_Output
PA6.GPIO_Label=JP34-ACtransfrmr
PA6.Signal=ADCx_IN6
PA7.GPIO_Label=PWR12V+
PA7.Signal=ADCx_IN7
PA8.GPIO_Label=OC3
PA8.Signal=S_TIM1_CH1
PA9.GPIO_Label=OC1
PA9.Signal=S_TIM1_CH2
PB0.GPIO_Label=STRING-PLUS
PB0.Signal=ADCx_IN8
PB1.GPIO_Label=STRING-MINUS
PB1.Signal=ADCx_IN9
PB10.Signal=S_TIM2_CH3
PB12.GPIO_Label=LED5-GRN
PB12.Signal=GPIO_Output
PB13.GPIO_Label=LED6-RED
PB13.Signal=GPIO_Output
PB14.GPIO_Label=OA4
PB14.Signal=S_TIM12_CH1
PB15.GPIO_Label=OA2
PB15.Signal=S_TIM12_CH2
PB2.GPIO_Label=HDR-OA3
PB2.Signal=S_TIM2_CH4
PB3.GPIO_Label=JP21-FETSUB104
PB3.Signal=S_TIM2_CH2
PB4.GPIO_Label=JP14-IN
PB4.Signal=GPIO_Input
PB5.Signal=CAN2_RX
PB6.Signal=CAN2_TX
PB8.Signal=CAN1_RX
PB9.Signal=CAN1_TX
PC0.GPIO_Label=JP9-THERM
PC0.Signal=ADCx_IN10
PC1.GPIO_Label=JP8-THERM
PC1.Signal=ADCx_IN11
PC10.Signal=USART3_TX
PC11.Signal=USART3_RX
PC12.Signal=UART5_TX
PC13.Signal=RTC_AF1
PC14-OSC32_IN.Signal=RCC_OSC32_IN
PC15-OSC32_OUT.Signal=RCC_OSC32_OUT
PC2.GPIO_Label=JP10-THERM
PC2.Signal=ADCx_IN12
PC3.GPIO_Label=JP11-THERM
PC3.Signal=ADCx_IN13
PC4.GPIO_Label=JP17-SPARE
PC4.Signal=ADCx_IN14
PC5.GPIO_Label=JP24-Pressure
PC5.Signal=ADCx_IN15
PC6.GPIO_Label=OB3
PC6.Signal=S_TIM3_CH1
PC7.GPIO_Label=OB1
PC7.Signal=S_TIM3_CH2
PC8.GPIO_Label=OB2
PC8.Signal=S_TIM3_CH3
PC9.GPIO_Label=OB4
PC9.Signal=S_TIM3_CH4
PD2.Signal=UART5_RX
PH0-OSC_IN.Signal=RCC_OSC_IN
PH1-OSC_OUT.Signal=RCC_OSC_OUT

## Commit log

2022-12-22 Add initial files
    [bmsmot.brd, bmsmot.sch, hv-divider-filter.ods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]
2023-03-25 save and backup
    [bmsmot.brd, bmsmot.sch]
2023-03-27 save and backup pcb work
    [bmsmot.brd, bmsmot.sch]
2023-03-28 save work. updating 12v controls
    [bmsmot.brd, bmsmot.sch]
2023-03-29 save and back work
    [bmsmot.brd, bmsmot.sch]
2023-03-30 save and backup. Added battery string float detection
    [bmsmot.brd, bmsmot.sch]
2023-03-31 sub-pwrfet update
    [bmsmot.brd, bmsmot.sch, pwrfet.brd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]
2023-04-03 Minor additions to pcb and documentation
    [bmsmot.brd, bmsmot.sch]
2023-04-09 update and save
    [bmsmot.brd, bmsmot.sch]
2023-04-10 changed pcb so BMS 12v not switched. Added sense to wake-up header.
    [bmsmot.brd, bmsmot.sch]
2023-04-20 save latest version of eagle layout. Adds 74VHCT125 and DFN2020 fets, plus other changes
    [bmsmot.brd, bmsmot.sch]
2023-04-22 bmsmot pcb part renumbered
    [bmsmot.brd, bmsmot.sch]
2023-04-23 some renaming of headers
    [bmsmot.brd, bmsmot.sch]
2023-04-23 updated LM2596 switcher to two sizes on pcb
    [bmsmot.brd, bmsmot.sch]
2023-04-24 more pcb updates
    [bmsmot.brd, bmsmot.sch]
2023-04-25 change flyback diode arrangement to select one diode with header
    [bmsmot.brd, bmsmot.sch]
2023-04-30 Added offset ADC input for measuring AC via 12v secondary on a transformer for the EMC-MMC configuration
    [bmsmot.brd, bmsmot.sch, pwrfet.sch]
2023-05-01 updates to pcb
    [bmsmot.brd, bmsmot.sch]
2023-05-07 added spi and i2c to L431
    [bmsmot.brd, bmsmot.sch]
2023-05-14 update bmsmot pcb
    [bmsmot.brd, bmsmot.sch, pwrfet.brd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]
2023-05-15 update pcb eagle files
    [bmsmot.brd, bmsmot.sch, pwrfet.brd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]
2023-05-17 update check
    [bmsmot.brd, bmsmot.sch, pwrfet.brd]
2023-06-26 bmsmot-v1 updates. emcmmc added. F446 and L431 led morse_trap working. Much more to do.
    [adcsetup.ods, bmsmot.brd, bmsmot.sch]
2023-06-27 yprintf working on both F446 and L431. ADC on L431 sequence running but not tested
2023-10-23 Working out bugs in RYTast
    [ADC-timing.ods, Processor-current.ods]
2023-10-28 relay pull-in test
2023-10-31 adding functions. work on adc
    [ADC-timing.ods]
2023-11-14 save and backup work
    [ADC-timing.ods]
2023-11-15 added ods files
    [Relay-mxuteuk.ods, adc-sumsquares.ods, resistor-offset-ac-into-adc.ods]
2023-12-03 adc2 cycles parameterized
    [ADC-timing.ods]
2023-12-04 add ADC docs
2023-12-05 added filter to offset and main to check that it works
2023-12-09 save work. memory-memory dma experiment with saving ADC2 raw readings to an array.
2023-12-12 save work on adc1 output
    [ADC-timing.ods]
2023-12-15 begin eagle sub-pwr-fet-v2 layout
    [pwrfet.brd, pwrfet.sch]
2023-12-19 pwrfet subboard v2 work
    [pwrfet.brd, pwrfet.sch]
2023-12-20 latest tweaks to sub-pwrfet-v2
    [pwrfet.brd, pwrfet.sch]
2023-12-21 added sub-pwrfet-v3 using ADP3120 FET driver. v2 uses GDG0543
    [pwrfet.brd, pwrfet.sch]
2023-12-28 pwrfet-v4 added but layout not complete
    [pwrfet.brd, pwrfet.sch]
2023-12-30 add sub-pwrfet-v4, which has gates and comparator for current limiting
    [pwrfet.brd, pwrfet.sch]
2023-12-30 updates to v4 subboard
    [pwrfet.brd, pwrfet.sch]
2024-01-06 pwrfet-v4 update
    [pwrfet.brd, pwrfet.sch, resistor-offset-ac-into-adc.ods]
2024-01-07 save latest tweaks of pcbs
    [pwrfet.brd, pwrfet.sch]
2024-01-18 update pwrfet designs
    [pwrfet.brd, pwrfet.sch]
2024-02-19 lastest with v6 order
    [pwrfet.brd, pwrfet.sch]
2024-03-07 update bmsmot-v1 to add PA4 adc of RSP power input voltage and option on encoder to monitor system12v CAN voltage
    [bmsmot.brd, bmsmot.sch]
2024-03-08 save work. Debugging motor ramping
2024-03-10 save motor ramping work
2024-03-11 motor control may work, but needs further testing
2024-09-11 changed const table for CAN id lookup to include a CAN id remap to avoid multiple lookups. a
    [StringChgrTask.c, StringChgrTask.h, stringchgr_items.c]
2024-09-16 added missing BMS timeout
    [StringChgrTask.c, StringChgrTask.h, main.c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]
2024-10-21 major revisions for ELCON charging. Compiles only
2024-11-04 update eagle files
    [bmsmot.brd, pwrfet.brd]
2024-11-05 update bmsmot eagle files
    [bmsmot.brd]
2025-05-10 save string charger work. Discovery phase seems-to-work
2025-11-10 add kicad directory with conversion from eagle 4 to eagle 6.5 to kicad
    [bmsmot.kicad_pcb, bmsmot.kicad_sch, bmsmot_1.kicad_sch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]

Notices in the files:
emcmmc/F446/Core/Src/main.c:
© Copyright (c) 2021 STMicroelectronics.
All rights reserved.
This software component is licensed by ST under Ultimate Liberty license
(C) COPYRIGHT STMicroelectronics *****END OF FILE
